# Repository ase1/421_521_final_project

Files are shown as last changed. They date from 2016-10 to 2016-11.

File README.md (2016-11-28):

# Kenny Toastman and Andrew Crusty present: [LaserToasterino](http://www.naminum.com/append?q=laser%20toaster)
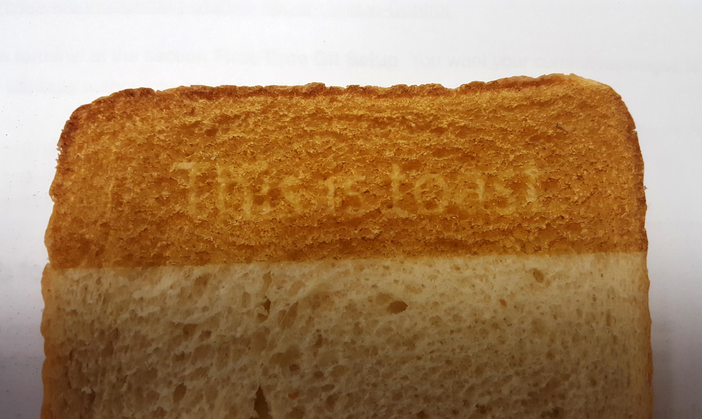
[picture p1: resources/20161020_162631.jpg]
This is toast.


This repository contains source code, CAD files, course deliverables, and instructions to create a laser toaster using a slew of microcontrollers. This is our final project for BIOE 421 at Rice University, taught by Dr. Jordan Miller and trusty assistant Dan Sazer. 

### Table of Contents
1. [Abstract] (#abstract)
2. [Use Flowchart] (#flowchart)
3. [Software Approach] (#software)
4. [Hardware Approach] (#hardware)
5. [Brainstorming] (#brainstorming)
6. [Safety] (#safety)

<a name="abstract">
### Abstract
Technological breakthroughs in the last decade have significantly altered the way we experience our everyday lives, from smartphones, smart TV's, and even IoT products like thermostats. One aspect of our lives, though, has not seen any improvements coming from technology for many decades-- toast. The goal of this project is to thrust the breakfast experience into the 21st century. We will create a device that allows you to wake up to a perfect piece of personalized toast. Laser etching will be used to burn images, a daily agenda, an inspirational quote, or the day’s headlines right onto a piece of bread. The device can be used immediately on command, or can be scheduled to have your perfect toast ready for you, right when you wake up. The image to be printed could be a selfie (or other inferior photo) that you upload or content from the Internet, allowing for an entirely customizeable breakfast.

The device will be comprised of a laser, an enclosure with controls, and a Raspberry Pi retrofitted onto an old 3D printer. Stepper motors will control the position of the laser along the toast, and the power of the laser will be modulated at each point to create different toasting patterns. Software will be developed to combine photos, Web-scraped text, and more into a grayscale image to be burned on the toast, and it will then generate G-code for printing. This project will aim to recreate the toaster experience using an Arduino to control the knobs, dings, and doors that we’ve all grown to love.

<a name="flowchart">
### Use Flowchart
This flowchart shows the processes and decisions that are made to output the admittedly scrumptious final product. 
Flowchart Flowchart showing use cases.

<a name="software">
### Software Approach
The three main facets of the software are controlling the motors/laser, generating and processing images for toasting into G-code, and displaying a graphical user interface to allow the user to select what they want on their toast. 

The GUI is the central hub of the software, connecting all of the pieces together. It runs in the Processing Development Environment, and monitors the touchscreen for button presses and acts accordingly. Each button is hardcoded because we didn't want to waste time making something fancy - we just need something that works. The GUI was laid out in Microsoft PowerPoint, then the layout was transferred over to Processing by determining all of the button sizes and locations. Screenshots of the GUI (running on a separate computer) are below: 

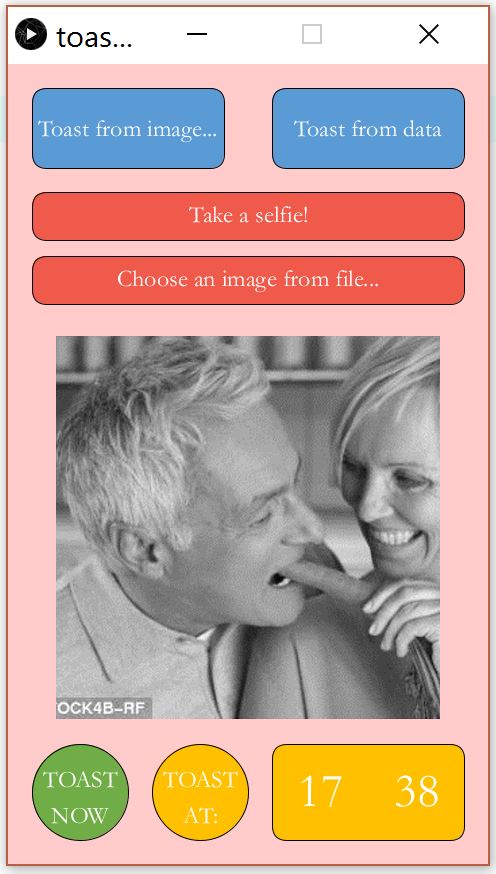
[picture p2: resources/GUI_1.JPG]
GUI1 Toast from an image...

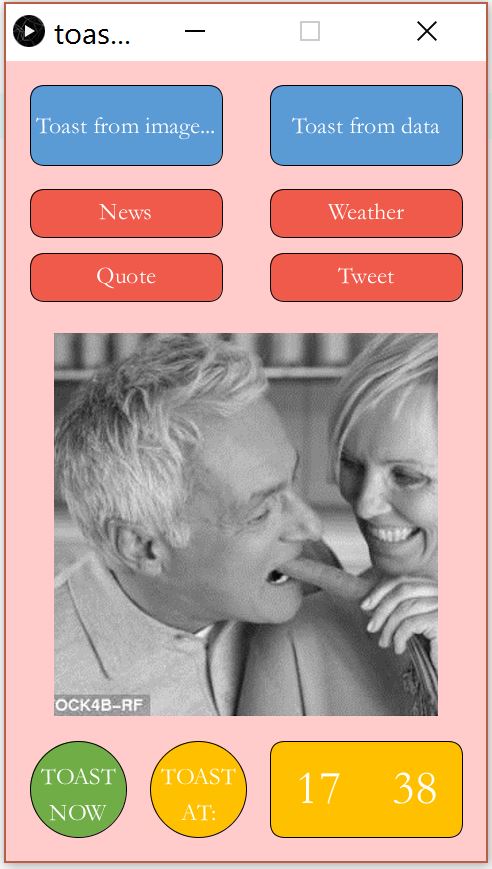
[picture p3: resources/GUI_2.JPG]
GUI2 Toast from data...

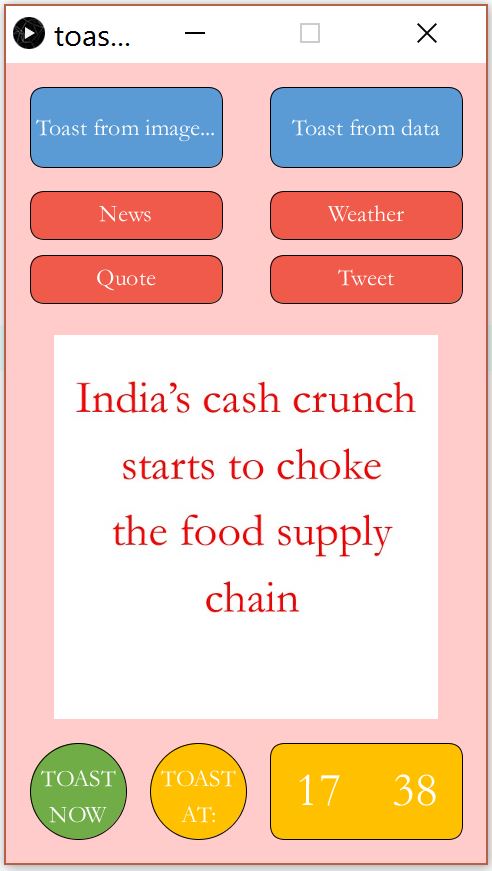
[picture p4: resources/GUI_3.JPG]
GUI3 Toast from data, populated


The GUI forces the user to follow the steps on the flowchart above, first prompting the user to either choose to toast from image or data, then prompting the user to select the specific pattern to toast. The user can either take an image using the Raspberry Pi camera, or use an existing file by navigating through the file browser. The toast from data option grabs the latest tweets from Twitter based on the selection, and formats the text as an image. The user then opts to immediately send the image to the toaster for processing and toasting, or to wait until the specified time. 

Each button press runs a bunch of scripts. We're using the launch() function in Processing, and launching .desktop files that run bash scripts that either run terminal functions or Python scripts. It's a really roundabout way of doing things, but it's the way we've been able to make Processing work for us. Variables for other scripts (like the image path, scheduled time, or status of the emergency stop button) are stored in dedicated text files. We chose to use Processing for the GUI environment because we want to integrate Arduino StandardFirmata and also want to make an attractive layout for the touchscreen. 

Once a user is ready to make his toast, he initiates a printing sequence by selecting the "Toast Now" button on the GUI. This actuates a series of steps that lead to printing, all executed in Python:

1. *Image Processing:*
  * Image resized to 128 x 128 pixels, which are the dimensions of the print (these numbers could change based on testing)
  * Image recolored to grayscale with lighter colors corresponding to darker pixels
    * This is so that lighter images will be more toasted
    * RGB values are converted to grayscale using a weighted average formula: I = .299[R] + .587[G] + .114[B]
  * Grayscale values are scaled to a power level 0-255, corresponding to the PWM range of the RAMBo Fan MOSFET output
    * Scaling is also based on the user's deisred toast power level (provided through the potentionmeter knob and Arduino)
    
2. *Automatic G-Code Generation:*
  * Based on the printer's print-area coordinates, the code generates a path for the laser head that covers each pixel in the image
  * At each pixel, the laser intensity changes corresponding to the intensity at that pixel
  * At the end of the print, the platform returns the toast to the user.
  * The G-Code is generated and saved as a .gcode file 
  
3. *Communicating with the Printer:*
  * We use Printcore, a software developed by Printrun (same group that makes Pronterface, Pronsole), to communicate with our RAMBo board.
    * Printcore is developed in Python and includes a module of commands that allow a user to interact with a printer
  * Connect with the printer through Serial Port, send over the G Code, and initiate print.
  * For safety, we also added the capability for a user to cancel the print mid-print, using the red "X" button in the GUI    

<a name="hardware">
### Hardware Approach
We have an old 3D printer, inherited from legendary Rice alum Ravi Sheth. We're using this as the base of our project since it already has the dimensional movement that our plotter will require. We want to take apart the printer, remove unnecessary components, and reassemble it inside of an enclosure. We need to install a couple of Arduino-controllable actuators to put some polish on the experience. For EHS reasons, we aren't allowed to use a laser powerful enough to cause blindness, so as a proof of concept, we'll mount a 5mW laser on the machine and test using photographic paper. 

The modified 3D printer hardware was modelled in SolidWorks, and the enclosure was created around it. The enclosure is made of plywood, which is fine for now because the laser isn't powerful enough to burn through it. It was made in the OEDK woodshop, and the display panel was ironically cut using a lasercutter. For the interface with the user, we're using a Raspberry Pi touchscreen display and a couple buttons and knobs for tactile control. A sliding door will shield the user from the laser during operation. 

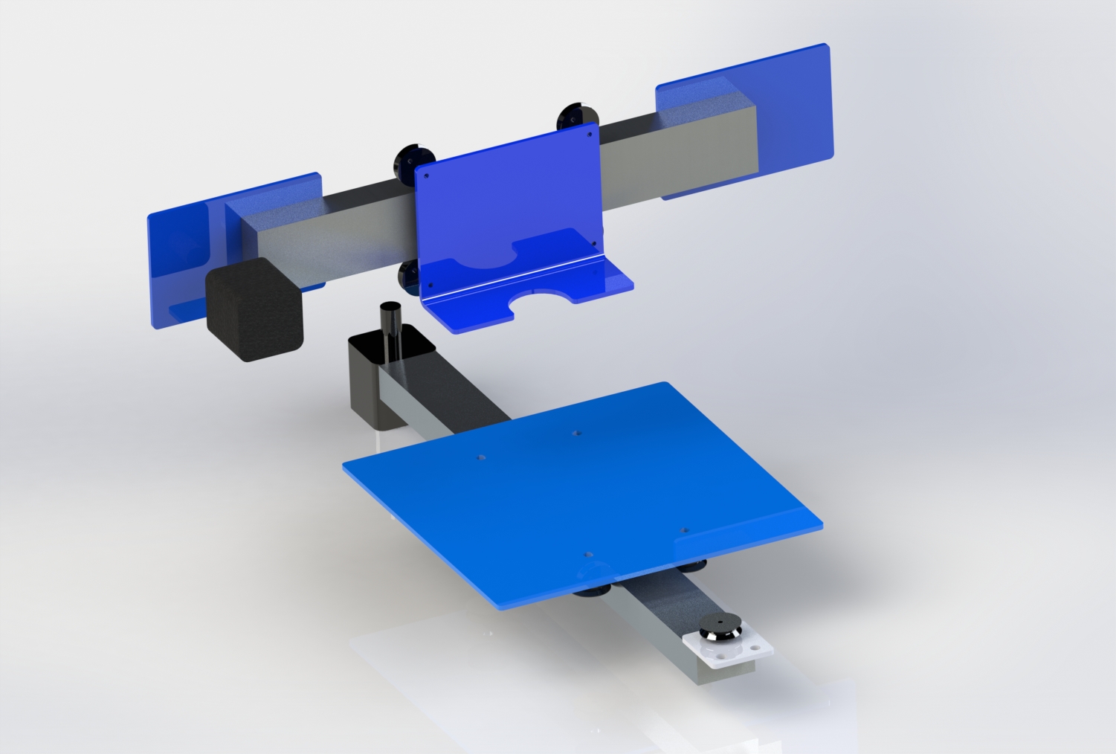
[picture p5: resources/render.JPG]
rendering The salvaged 3D printer parts


On the electrical side, we'll be using three boards for this project: a Raspberry Pi, a RAMBo motherboard, and an Arduino Uno. We had a bunch of problems hooking up the laser to the RAMBo; the idea was to control the intensity using the 12V PWM slot for cooling fans, but the fuses on the board kept burning out when our 5V lasers were connnected. We made a linear voltage regulator circuit to control the input voltage to the laser diode, and it seems to be more stable now. Both the Arduino and the RAMBo communicate with the Raspberry Pi using a serial connection. The Pi connects directly to the touchscreen and uses that as the only display. Ideally, the keyboard and mouse will be unnecessary to run the printer. 

<a name="brainstorming">
### Brainstorming
We spent the weekend coming up with ideas, and the crowd favorite is a toast printer. You've seen Jesus toast, and we want to take that one step further. Imagine waking up, checking your calendar, reading the newspaper, and ravenously scrounging for something to eat in the morning. Our idea proposes to combine early morning activities using a toaster with a controllable toast pattern. We're considering creating an appliance that internally works like a laser etcher, with the functions of a toaster. We have a non-working 3D printer that we're willing to scavenge for parts. We plan to design the hardware and software experience. Software for generating G-code for laser etching already exists, so we'd probably implement that and focus our efforts on image processing, content production, and hardware control. 

 - Sensors: 
   - Check if bread is on the plate
   - Check door status (open/closed)
   - Check power level dial
   - Button for start
   - Laser temperature

 - Actuators: 
   - Emergency stop button
   - Eject button (might be fun to have this under a plastic shield)
   - Must include spring actuation and self-deployed toast parachute
   - Move platform
   - Open/close door
   - Ring bell when complete
   - Laser ventilation
   - Alarm clock function that wakes you up to fresh toast

 - If we have time (we won’t have time):
   - Toast flipper
   - Camera on toast (timelapse?) (Twitter?)
   - Butter melter and liquid butter spreader
   - Photo booth

##### Discrete subprojects: 
 - Create lasercutter functionality - hardware
   - Disassemble printer
   - Buy parts
   - Figure out power requirements
   - Safety measures
   - Control 
 - Data grabbing from the internet
   - Date
   - Inspirational quotes
   - News
   - Notifications
 - Compile into an image for image processing
   - Image processing (see this: http://nebarnix.com/img2gco/)
   - Take existing image and convert to grayscale
   - Create an array of laser voltages per pixel
     - We can just always go line-by-line if that’s easier
   - Send to laser cutter
   - Arduino stuff

<a name="safety">
### Safety (for a device with a full-powered laser)
We can break safety concerns down to three categories: health, fire, and electrical. 

__Health__. The most threatening safety concern is health - pointing a laser at a person for too long could cause blindness or burns. The easiest countermeasure is to buy the lowest-powered laser that will still accomplish our goal. We're ready to do some testing on Thursday using the OEDK laser cutter to see what powers we realistically need for etching the toast, but online research has shown that we won't need more than 1-2 W. For testing, we'll want to modulate that power down to the mW range (typical laser pointers are 5-10 mW) so we can see what we're doing but aren't creating any threat. The final device will have a door that seals the inside off from the outside, so there can be no leakage of light. We can make this door into a physical switch, so the laser can't receive power unless this door is closed. For testing, we'll also have to get some laser safety glasses, which depend on the wavelength of light produced by the laser. 

__Fire__. Another big one, also mostly solved by choosing the right laser. We want to do some testing on the laser that we eventually choose, but if need be, we can solder on a heatsink and provide forced convection with a fan. I don't expect there to be too much smoke produced, since normal toasters don't produce an unreasonable amount of smoke and we plan to only etch the surface of the toast. We want to make the enclosure out of think aluminum or 1/4" wood - the laser shouldn't be high-powered enough to penetrate or ignite either of these. 

__Electrical__. Good insulation practices should resolve any concerns.

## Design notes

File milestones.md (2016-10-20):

# Toastr (name pending) Milestones
Andrew Elsey, Kenny Groszman
BIOE 421

Here we will outline our deadlines that we hope to accomplish in order to finish this project on time.

### Class Due Dates:
 - Abstract : 11/3
 - Initial Proof of Concept Prototype : 11/10
 - Fit and Finish : 11/17
 - Final project Due : 11/29

Milestones:

 - 10/27 :
   - CAD Model of Hardware and generate list of parts to acquire (Andrew)
   - Image processing software (Kenny)
      - Importang an image, resizing it, converting to grayscale, exporting matrix of power levels
   - Take apart 3D printer
   - Lay out structure of software and what functions we need, how they fit together, etc.

 - 11/3 : 
   - Hardware: Retrofit laser to printer,  control location of laser using motors and necessary software, build enclosure
   - Software: generate the software that allows us to modulate motors and laser power
   - Finalize abstract (due 11/3!)

 - 11/10 : 
   - Go to EHS laser safety meetings?????????? on 11/4
   - Implement actuators and sensors (knobs, buttons, switches, dingy speaker)
   - Begin work on GUI
   - Try data scraping from the internet!
   - MUST HAVE INITIAL PROTOTYPE DUE BY 11/10

 - 11/17
   - Error handling
   - Streamline GUI
   - Turn in fit and finish, whatever that is
   - Try photopapaer experiments

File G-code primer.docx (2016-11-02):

GCODE Primer for Laser Cutter Control

General Information

Gcode is a very simple code designed to control 3D printers. We have an adapted version of a GCODE interpreter courtesy of Tim Schmidt from the Lansing Makers Network (https://github.com/lansing-makers-network/buildlog-lasercutter-marlin) that has been augmented to better control laser based machines like our laser cutter.

The flow of Gcode is fairly simple. Commands are given line by line with appropriate arguments. For example, a typical move command would look like this:

“G0 X1 Y2 Z3 F1000”

The initial command G0 specifies the function G0 to be applied. The following arguments are comprised of an initial letter to describe the type of argument, and a numerical value to quantify the argument. For example, the letters X, Y, and Z denote coordinates in the X, Y, and Z directions respectively. The numbers following X, Y, and Z show the coordinate value to move towards. The F value is a different argument, which specifies the movement speed. So 1000 quantifies how fast to move for this variable.

The Gcode RepRap wiki (http://reprap.org/wiki/G-code) gives a fairly comprehensive list of Gcode commands and appropriate descriptions. There are different Gcode interpreters including our interpreter (Marlin).

Interpreter firmware/Gcode syntax has been extensively used by the RepRap community to simplify the ability to control 3D printing movement. It is important to note though, that Gcode simply encodes for firing of electrical pulses in a predefined manner. So, even though Gcode was not designed for controlling a laser cutter, commands can be co-opted for unorthodox uses if the controller board is correctly wired to the laser cutter.

Below is a list of Gcode commands specific to our laser cutter/Marlin firmware setup with accompanying arguments and descriptions.

Important Commands for Controlling our Firmware

  - M649
    - Set Laser Fire Settings
    - Arguments
      - S
        - Laser Intensity
        - Values are 0 to 100 (float type)
        - Units are % laser power
      - L
        - Duration of laser pulse
        - Values are integers
        - Units are microseconds (μs)
      - P
        - Pulses per millimeter
        - Values are float type
        - Resolution discussed below
      - B
        - “Beam type”
        - 0 for continuous fire
        - 1 for Pulsed (note: specifying “P” should automatically change to B1 mode)
        - 2 for raster mode
      - D
        - Diagnostics
        - Logical 0 or 1 for whether to output diagnostics
  - M3
    - Turn laser on with current laser settings
    - Laser settings can be specified with an M3 command, but if a setting is not specified, the previously used value will be used.
  - M5
    - *****Turn laser off
  - G0
    - Move without laser on
    - Behaves identically with old marlin Gcode
  - G1
    - Move with laser on
    - Uses previously stored laser settings
    - Can take arguments from M649 to customize laser settings
  - M114
    - Obtain current coordinates
    - Enter directly to pronterface
    - Can be input while printing without disrupting the current print
  - G92
    - Set Coordinates
    - Takes X, Y, and Z arguments
  - G90
    - Set absolute coordinates
    - G0/G1 commands with X, Y, and Z will specify absolute coordinate locations
    - i.e. if you enter G0 X1 Y2 Z3 twice, the first command will move to (1,2,3) and the second command will not move (because you are already at the specified locations)
  - G91
    - Set relative coordinates
    - G0/G1 commands with X,Y, and Z will specify a relative movement direction
    - i.e. G0 X1 Y2 Z3 twice will move in a <1,2,3> vector direction twice to a final destination of (2, 4, 6) relative to the initial position
  - M84
    - Turn motors off

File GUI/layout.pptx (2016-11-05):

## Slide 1

Toast from image

Toast from data

Take a selfie!

Choose image…

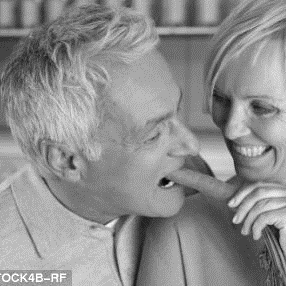
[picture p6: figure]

TOAST NOW

TOAST
AT:

08

15

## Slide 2

Toast from image

News

Agenda

Toast from data

Quote

Latest tweet from…

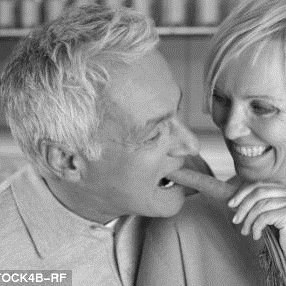
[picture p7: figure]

TOAST NOW

TOAST
AT:

08

15

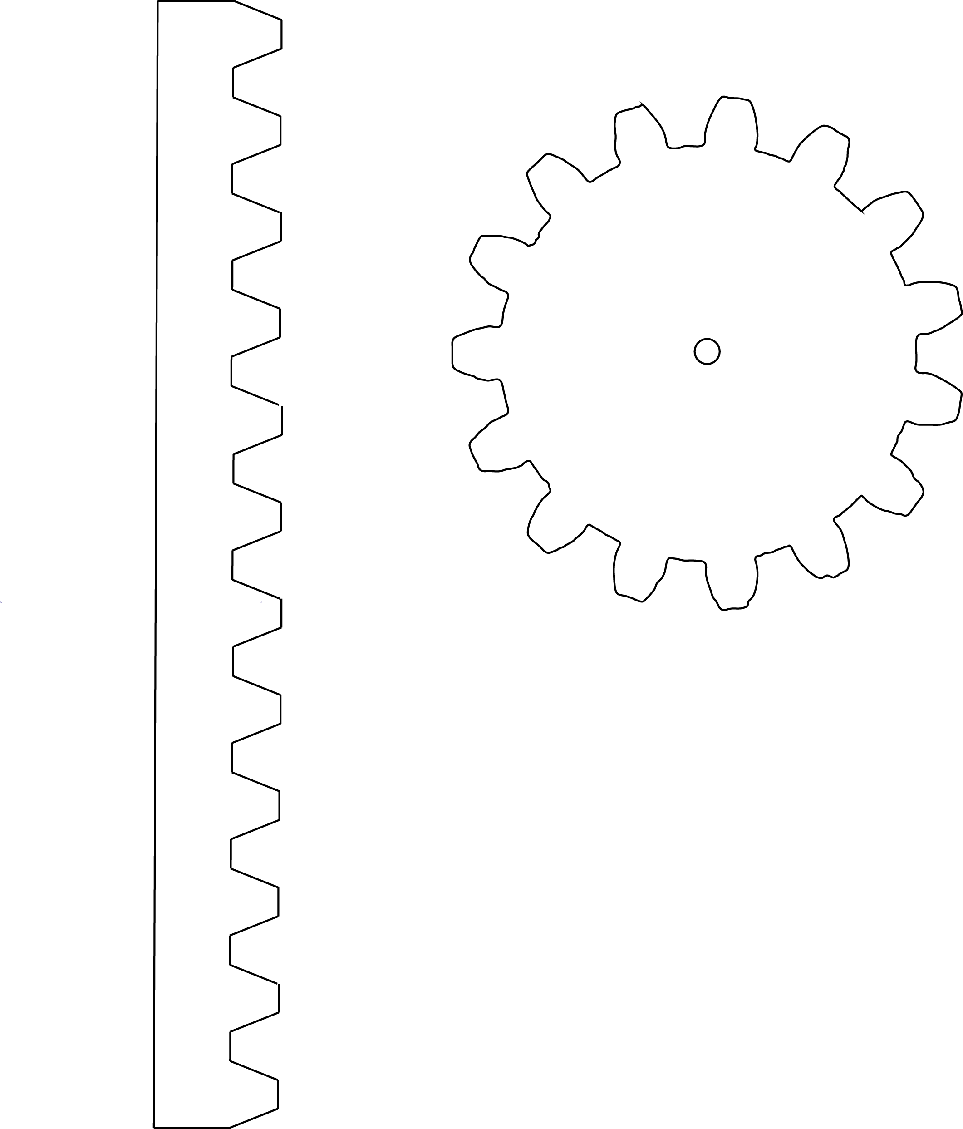
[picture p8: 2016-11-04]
Hardware/gears.png

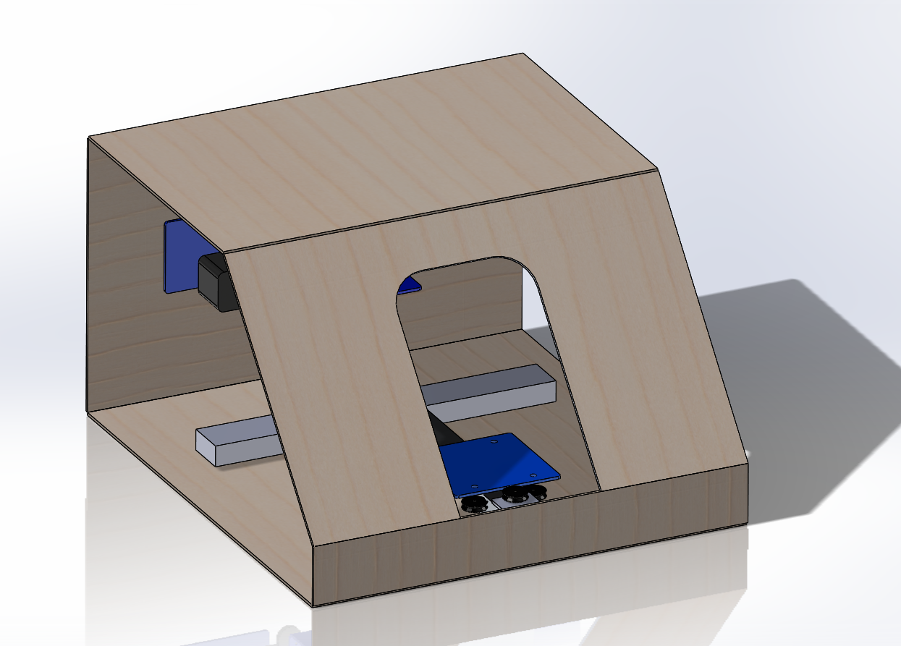
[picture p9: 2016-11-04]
Hardware/enclosure.PNG

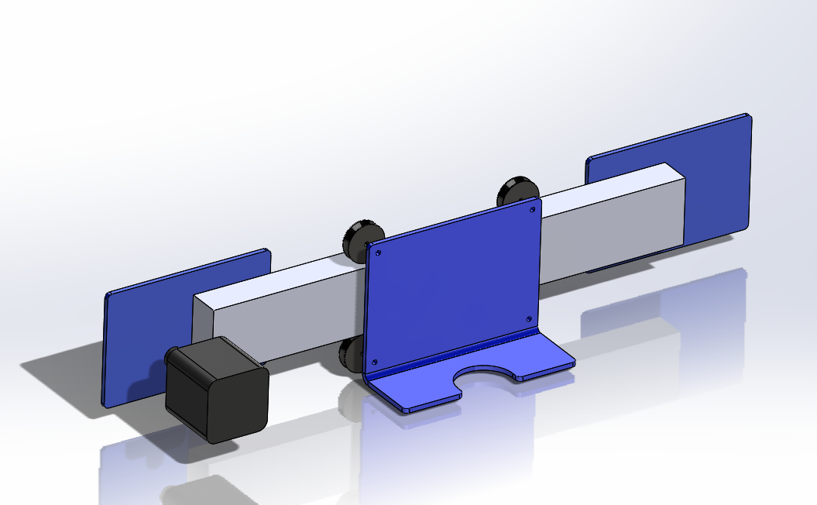
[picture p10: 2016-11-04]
Hardware/laser_assy.PNG

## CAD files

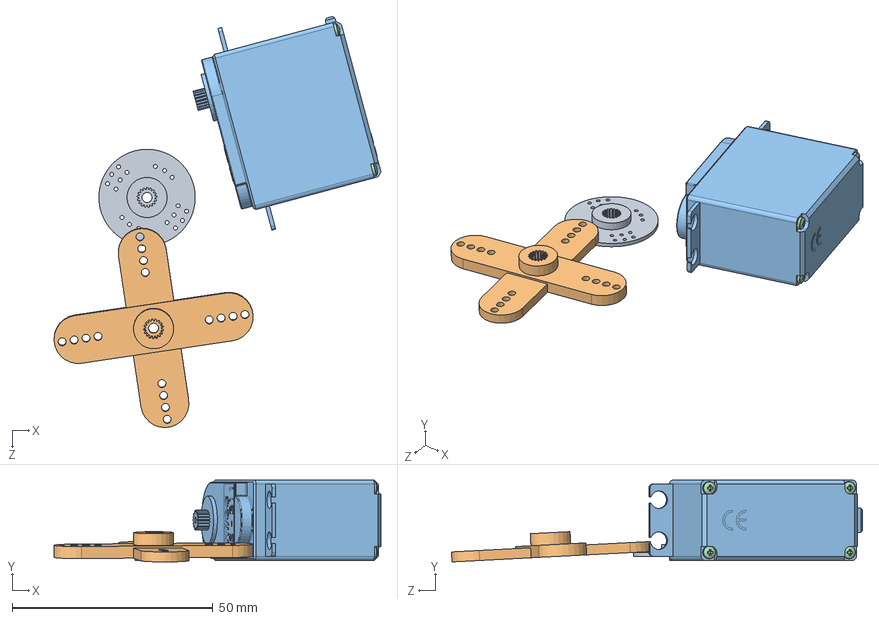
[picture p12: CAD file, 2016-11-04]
Hardware/Hitec HS-311 Servo Motor/Hitec HS-311.SLDASM
81.4 x 20.4 x 102.3 mm
Spline
Spline 2
Hitec Servo Motor HS-311
pan head cross recess screw_din x 4

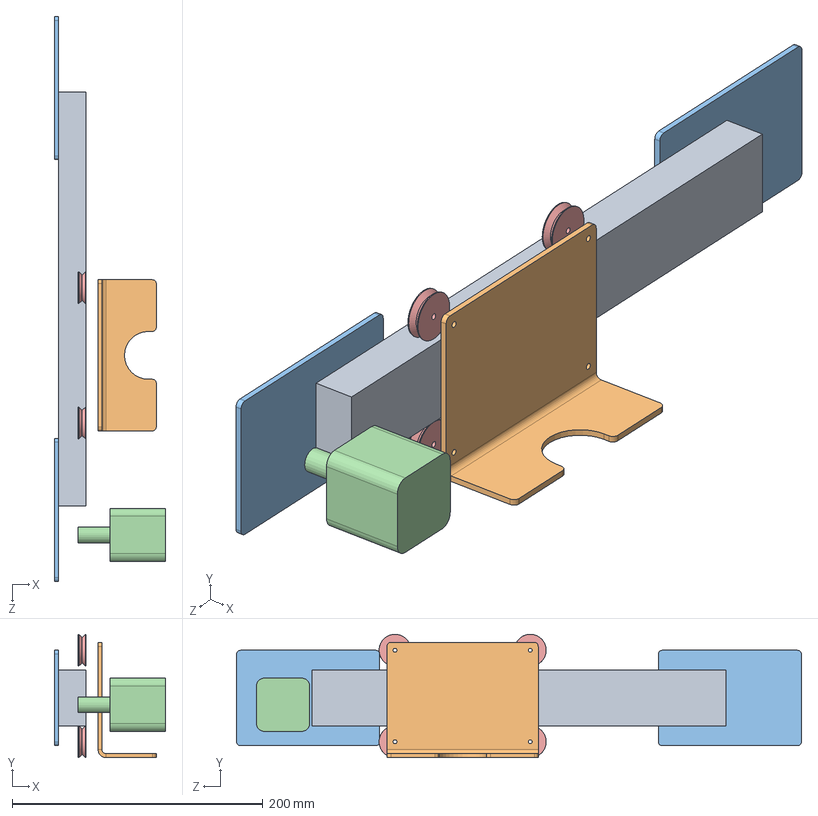
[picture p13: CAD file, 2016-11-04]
Hardware/laser_assy.SLDASM
88.9 x 98.4 x 450.9 mm
topchannel
lasermount
supportplate x 2
motor
bearing x 4

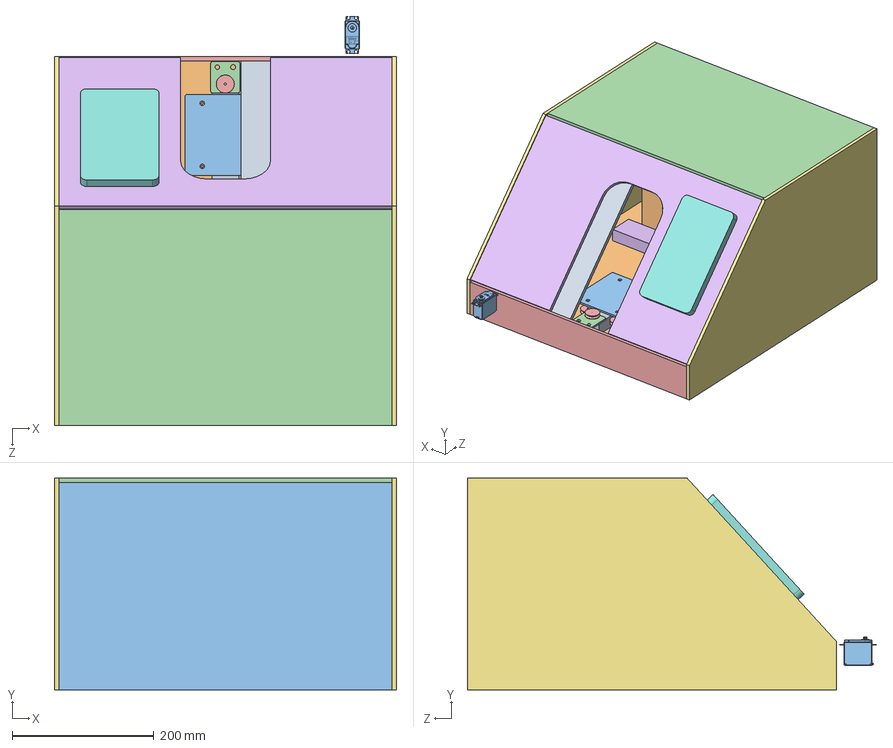
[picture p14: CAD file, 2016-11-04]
Hardware/full_assy.SLDASM
482.6 x 298.5 x 576.8 mm
bottomchannel
motor x 2
platformnew
frontplate
bearing x 9
basechannel
topchannel
lasermount
supportplate x 2
enc_base
enc_back
enc_top
enc_front
enc_display
enc_side x 2
raspi screen
enc_door
supportchannel x 2
Hitec Servo Motor HS-311

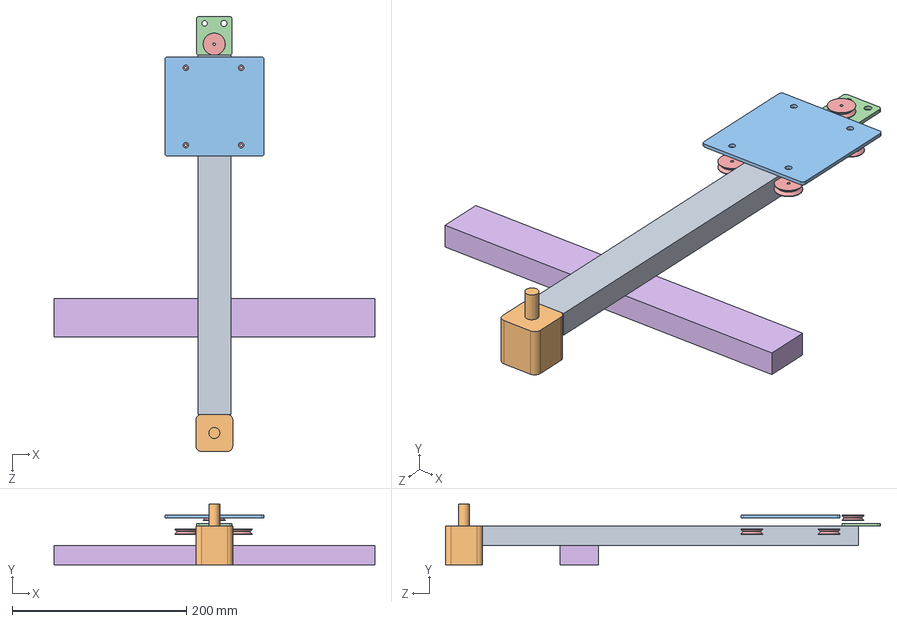
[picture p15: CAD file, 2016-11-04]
Hardware/bottom_assy.SLDASM
368.3 x 69.8 x 499.7 mm
bottomchannel
motor
platformnew
frontplate
bearing x 5
basechannel

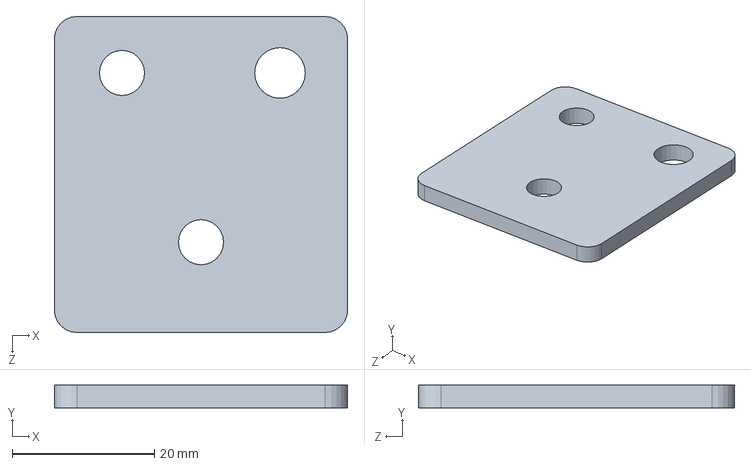
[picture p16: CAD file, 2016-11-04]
Hardware/frontplate.SLDPRT
41.3 x 3.17 x 44.5 mm

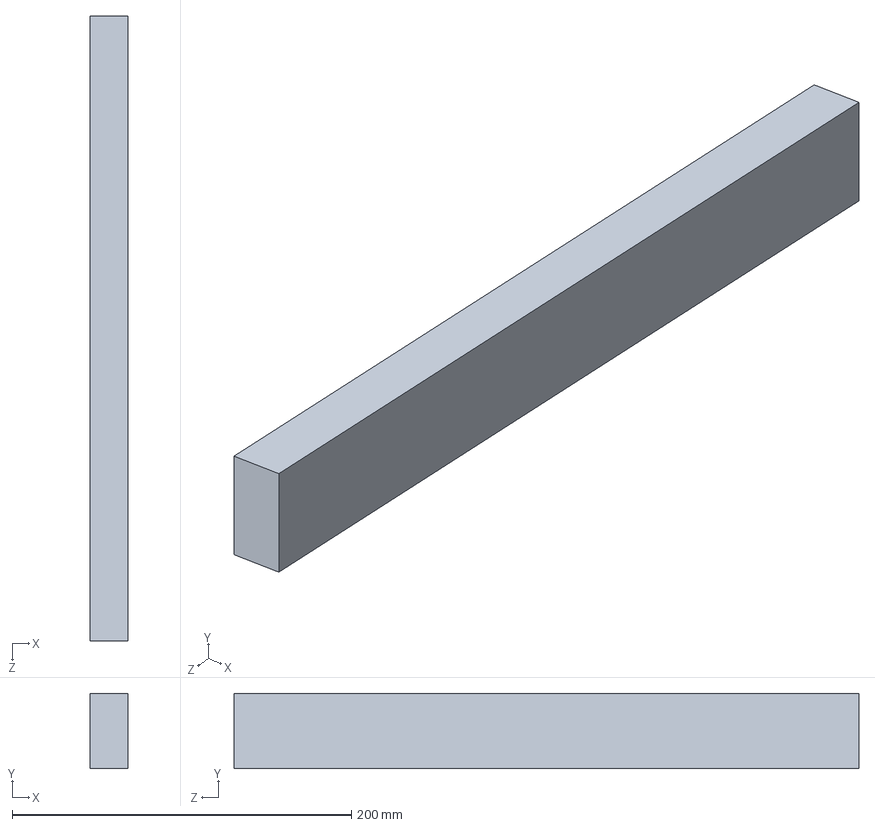
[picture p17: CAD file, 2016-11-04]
Hardware/basechannel.SLDPRT
22.2 x 44.5 x 368.3 mm

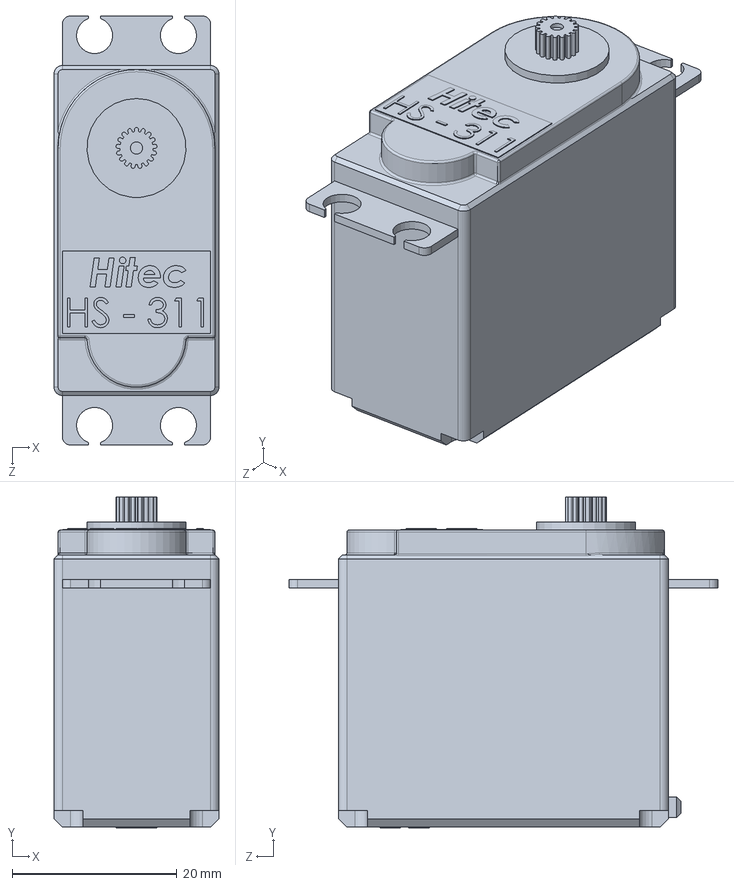
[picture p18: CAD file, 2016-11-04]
Hardware/Hitec HS-311 Servo Motor/Hitec Servo Motor HS-311.SLDPRT
20.0 x 40.1 x 52.0 mm

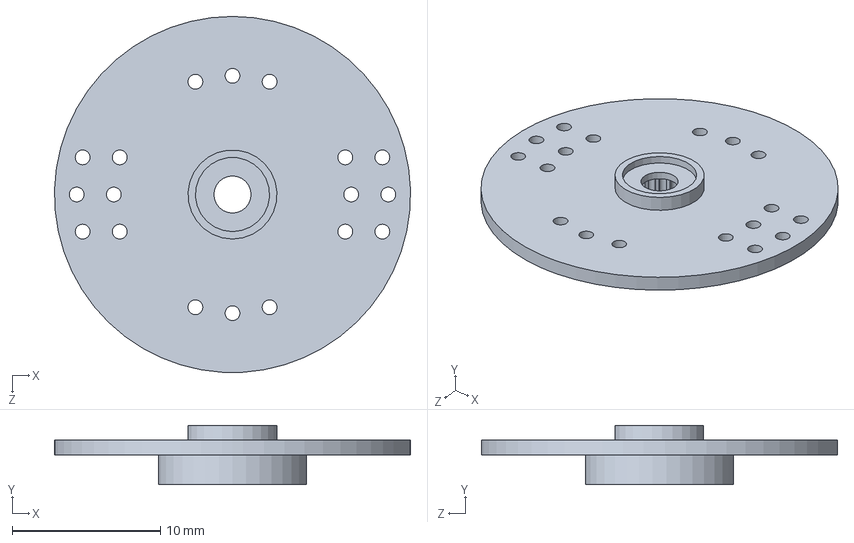
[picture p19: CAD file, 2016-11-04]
Hardware/Hitec HS-311 Servo Motor/Spline.SLDPRT
24.0 x 4.00 x 24.0 mm

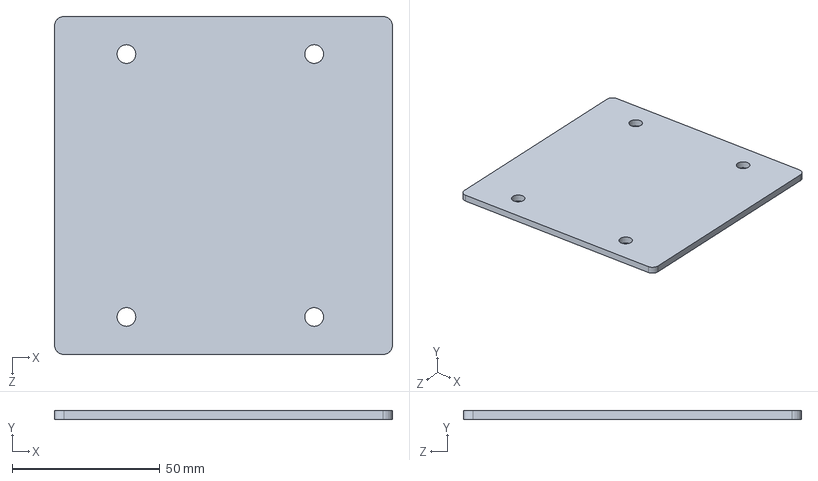
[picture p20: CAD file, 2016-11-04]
Hardware/platformnew.SLDPRT
114.3 x 3.17 x 114.3 mm

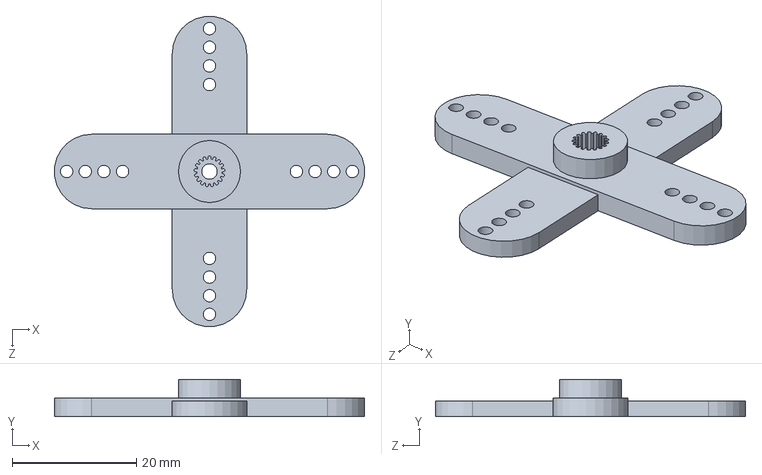
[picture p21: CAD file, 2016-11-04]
Hardware/Hitec HS-311 Servo Motor/Spline 2.SLDPRT
49.9 x 6.00 x 49.9 mm

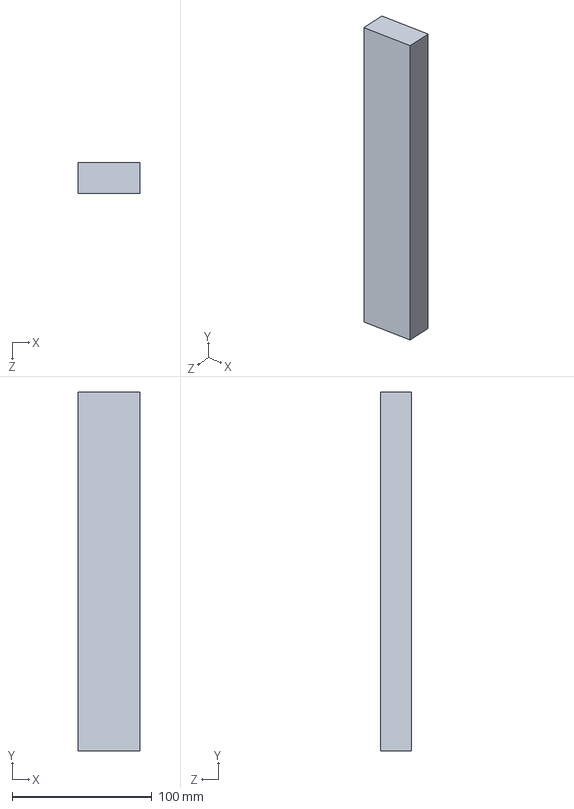
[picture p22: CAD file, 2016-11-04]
Hardware/supportchannel.SLDPRT
44.5 x 257.2 x 22.2 mm

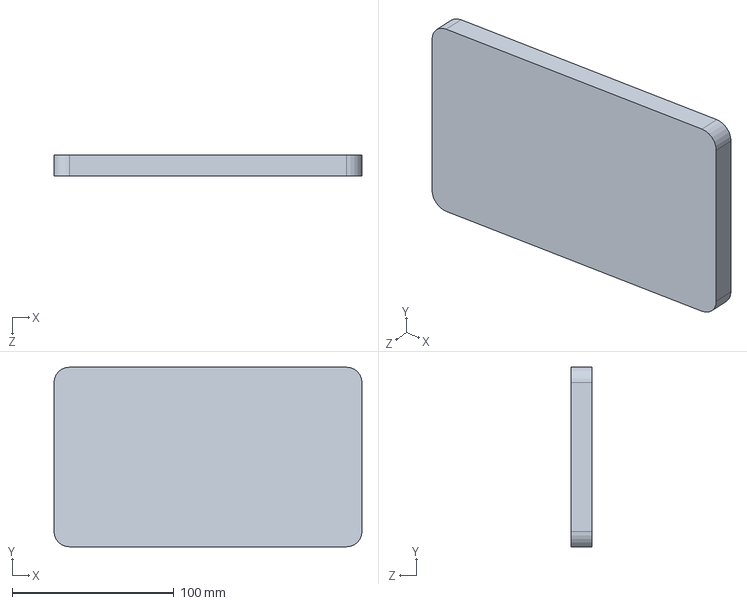
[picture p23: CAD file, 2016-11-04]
Hardware/raspi screen.SLDPRT
190.5 x 111.1 x 12.7 mm

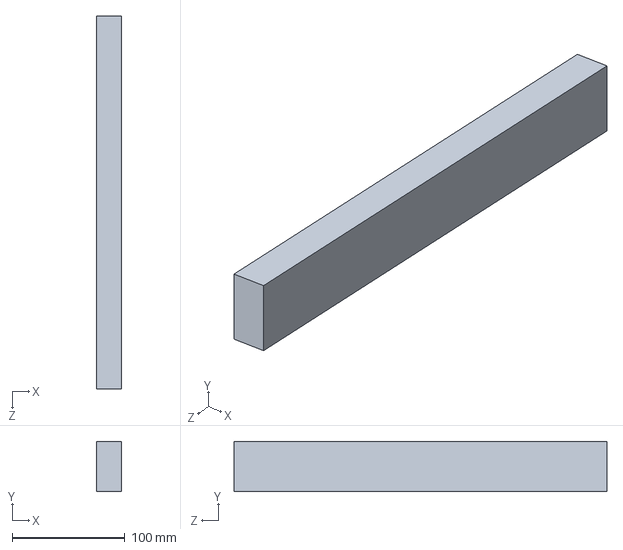
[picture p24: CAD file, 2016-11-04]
Hardware/topchannel.SLDPRT
22.2 x 44.5 x 330.2 mm

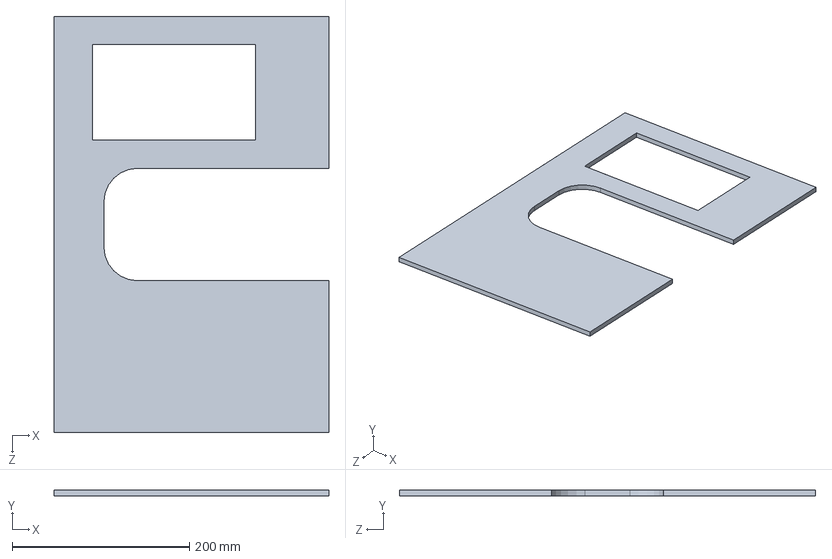
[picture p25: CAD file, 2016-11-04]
Hardware/enc_display.SLDPRT
310.1 x 6.35 x 469.9 mm

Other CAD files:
Hardware/enc_door.SLDPRT
Hardware/enc_front.SLDPRT
Hardware/supportplate.SLDPRT
Hardware/mount.SLDPRT
Hardware/bearing.SLDPRT
Hardware/bottomchannel.SLDPRT
Hardware/enc_back.SLDPRT
Hardware/enc_base.SLDPRT
Hardware/enc_side.SLDPRT
Hardware/enc_top.SLDPRT
Hardware/lasermount.SLDPRT
Hardware/motor.SLDPRT
Hardware/pinion.SLDPRT
Hardware/platform.SLDPRT
Hardware/rack_no_teeth.SLDPRT

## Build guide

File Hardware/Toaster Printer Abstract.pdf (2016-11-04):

Technological breakthroughs in the last decade have significantly altered the way we experience our everyday lives, from smart phones, smart TV's, and even IoT products like air conditioners. One aspect of our lives, though, that has not seen any improvements coming from technology for many decades-- toast. The goal of this project is to bring the breakfast experience to the 21st century. We will create a device that allows you to wake up to a perfect piece of personalized toast. Laser etching will be used to burn images, a schedule, an inspirational quote, or the day’s headlines right onto a piece of bread. The device can be set to act like an alarm clock, waking you up to your perfect toast, or used throughout the day. The image to be printed could be a selfie that you upload, data from relevant news websites, or updates from your favorite social media site, allowing for an entirely customizable breakfast.

The device will feature a laser, an enclosure with controls, and a Raspberry Pi retrofitted onto an old 3D printer. Stepper motors will control the position of the laser along the toast, with the power of the laser modulated at each point to create different toasting patterns. Software will be developed to combine photos, Web-scraped text, and more into a grayscale image to be burned on the toast, and process this image for printing. This project will aim to recreate the toaster experience using an Arduino to control the knobs, dings, and doors that we’ve all grown to love.

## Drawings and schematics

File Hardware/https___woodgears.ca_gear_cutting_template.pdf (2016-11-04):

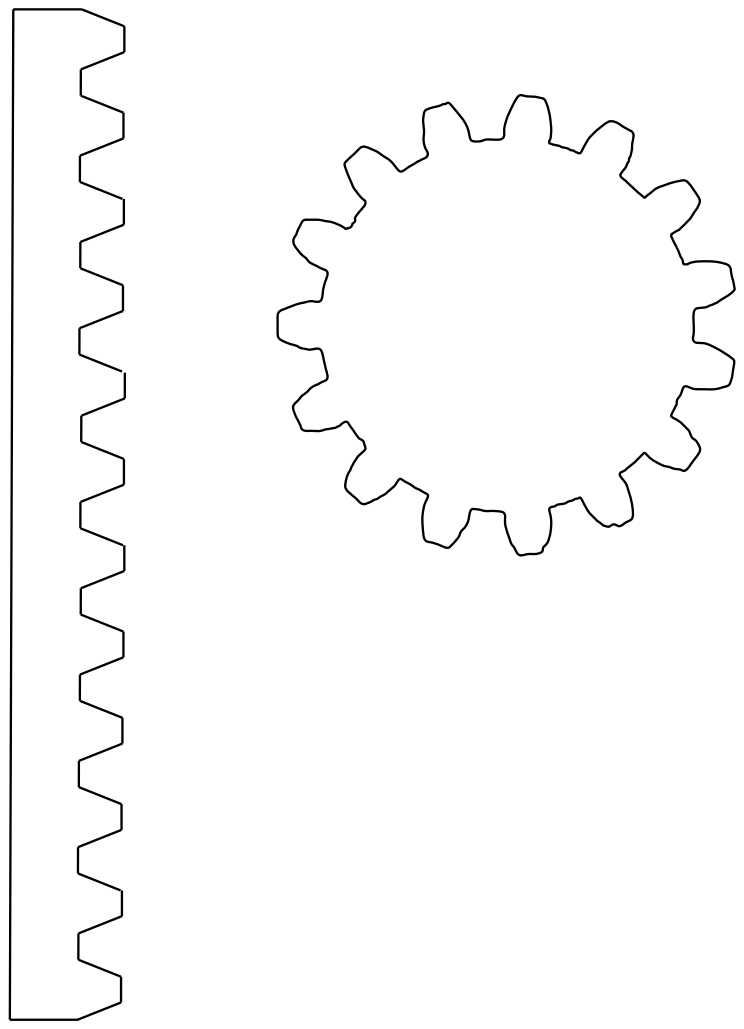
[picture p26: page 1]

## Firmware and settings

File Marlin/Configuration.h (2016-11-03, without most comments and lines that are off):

#define CONFIGURATION_H
#define STRING_VERSION_CONFIG_H __DATE__ " " __TIME__ // build date and time
#define STRING_CONFIG_H_AUTHOR "(ChenLab ShopBot Desktop D2418 by jmil, using Ultimachine RAMBo)" //Who made the changes.
#define SERIAL_PORT 0
#define BAUDRATE 250000
#define MOTHERBOARD 301
#define POWER_SUPPLY 1
#define TEMP_SENSOR_0 0
#define TEMP_SENSOR_1 0
#define TEMP_SENSOR_2 0
#define TEMP_SENSOR_BED 1
#define TEMP_RESIDENCY_TIME 10	// (seconds)
#define TEMP_HYSTERESIS 3       // (degC) range of +/- temperatures considered "close" to the target one
#define TEMP_WINDOW     1       // (degC) Window around target to start the recidency timer x degC early.
#define HEATER_0_MINTEMP 5
#define HEATER_1_MINTEMP 5
#define HEATER_2_MINTEMP 5
#define BED_MINTEMP 5
#define HEATER_0_MAXTEMP 275
#define HEATER_1_MAXTEMP 275
#define HEATER_2_MAXTEMP 275
#define BED_MAXTEMP 150
#define PIDTEMP
#define BANG_MAX 256 // limits current to nozzle while in bang-bang mode; 256=full current
#define PID_MAX 256 // limits current to nozzle while PID is active (see PID_FUNCTIONAL_RANGE below); 256=full current
  #define PID_FUNCTIONAL_RANGE 10 // If the temperature difference between the target temperature and the actual temperature
  #define PID_INTEGRAL_DRIVE_MAX 255  //limit for the integral term
  #define K1 0.95 //smoothing factor withing the PID
  #define PID_dT ((16.0 * 8.0)/(F_CPU / 64.0 / 256.0)) //sampling period of the temperature routine
    #define  DEFAULT_Kp 22.2
    #define  DEFAULT_Ki 1.08
    #define  DEFAULT_Kd 114
#define MAX_BED_POWER 256 // limits duty cycle to bed; 256=full current
#define PREVENT_DANGEROUS_EXTRUDE
#define PREVENT_LENGTHY_EXTRUDE
#define EXTRUDE_MINTEMP 170
#define EXTRUDE_MAXLENGTH (X_MAX_LENGTH+Y_MAX_LENGTH) //prevent extrusion of very large distances.
#define ENDSTOPPULLUPS // Comment this out (using // at the start of the line) to disable the endstop pullup resistors
  #define ENDSTOPPULLUP_XMIN
  #define ENDSTOPPULLUP_YMIN
  #define ENDSTOPPULLUP_ZMIN
const bool X_ENDSTOPS_INVERTING = false; // set to true to invert the logic of the endstops.
const bool Y_ENDSTOPS_INVERTING = false; // set to true to invert the logic of the endstops.
const bool Z_ENDSTOPS_INVERTING = false; // set to true to invert the logic of the endstops.
#define X_ENABLE_ON 0
#define Y_ENABLE_ON 0
#define Z_ENABLE_ON 0
#define E_ENABLE_ON 0 // For all extruders
#define DISABLE_X false
#define DISABLE_Y false
#define DISABLE_Z false
#define DISABLE_E false // For all extruders
#define INVERT_X_DIR true    // for Mendel set to false, for Orca set to true
#define INVERT_Y_DIR true    // for Mendel set to true, for Orca set to false
#define INVERT_Z_DIR true     // for Mendel set to false, for Orca set to true
#define INVERT_E0_DIR false   // for direct drive extruder v9 set to true, for geared extruder set to false
#define INVERT_E1_DIR false    // for direct drive extruder v9 set to true, for geared extruder set to false
#define INVERT_E2_DIR false   // for direct drive extruder v9 set to true, for geared extruder set to false
#define X_HOME_DIR -1
#define Y_HOME_DIR -1
#define Z_HOME_DIR -1
#define min_software_endstops false //If true, axis won't move to coordinates less than HOME_POS.
#define max_software_endstops true  //If true, axis won't move to coordinates greater than the defined lengths below.
#define X_MAX_POS 600
#define X_MIN_POS 0
#define Y_MAX_POS 475
#define Y_MIN_POS 0
#define Z_MAX_POS 90
#define Z_MIN_POS 0
#define X_MAX_LENGTH (X_MAX_POS - X_MIN_POS)
#define Y_MAX_LENGTH (Y_MAX_POS - Y_MIN_POS)
#define Z_MAX_LENGTH (Z_MAX_POS - Z_MIN_POS)
#define MANUAL_X_HOME_POS 0
#define MANUAL_Y_HOME_POS 0
#define MANUAL_Z_HOME_POS 0
#define NUM_AXIS 4 // The axis order in all axis related arrays is X, Y, Z, E
#define HOMING_FEEDRATE {50*60, 50*60, 50*60, 0}  // set the homing speeds (mm/min)
#define DEFAULT_AXIS_STEPS_PER_UNIT   {78.7402,78.7402,200.0*8/3,760*1.1}  // default steps per unit for ultimaker
 #define DEFAULT_MAX_FEEDRATE          {500, 500, 5, 25}    // (mm/sec)
 #define DEFAULT_MAX_ACCELERATION      {9000,9000,100,10000}    // X, Y, Z, E maximum start speed for accelerated moves. E default values are good for skeinforge 40+, for older versions raise them a lot.
 #define DEFAULT_ACCELERATION          3000    // X, Y, Z and E max acceleration in mm/s^2 for printing moves
 #define DEFAULT_RETRACT_ACCELERATION  3000   // X, Y, Z and E max acceleration in mm/s^2 for r retracts
 #define DEFAULT_XYJERK                20.0    // (mm/sec)
 #define DEFAULT_ZJERK                 0.4     // (mm/sec)
 #define DEFAULT_EJERK                 5.0    // (mm/sec)
#define PLA_PREHEAT_HOTEND_TEMP 180
#define PLA_PREHEAT_HPB_TEMP 70
#define PLA_PREHEAT_FAN_SPEED 255		// Insert Value between 0 and 255
#define ABS_PREHEAT_HOTEND_TEMP 240
#define ABS_PREHEAT_HPB_TEMP 100
#define ABS_PREHEAT_FAN_SPEED 255		// Insert Value between 0 and 255
#define BARICUDA
#include "Configuration_adv.h"
#include "thermistortables.h"

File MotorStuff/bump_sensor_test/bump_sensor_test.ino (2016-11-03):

int bump;

void setup() {
  // put your setup code here, to run once:
  Serial.begin(9600);           // set up Serial library at 9600 bps

  pinMode(2, INPUT);
  pinMode(3,OUTPUT);
  digitalWrite(2, HIGH);
}


void loop() {
  // put your main code here, to run repeatedly:
  bump=digitalRead(3);
  
  Serial.println(bump +" "+ digitalRead(2));
 
  
}

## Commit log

2016-10-20 Added lasered toast image
    "This is toast."
2016-10-27 add GIF of proof-of-concept moving motor
2016-11-02 update code to flatten image matrix in proper order for printing.
    Need to update to make it output G Code
2016-11-03 add original marlin firmware
    [Configuration.h, Configuration_adv.h]
2016-11-03 ADD NEW VERSION OF MARLIN THAT WORKS!!!!!!!!!!!!!!!!!!!!!!!!
    [Configuration.h, Configuration_adv.h]
2016-11-03 upload working MARLIN
    [Menu Plans.xlsx]
2016-11-03 added CAD files for the updated design
2016-11-04 extracted and filed the CAD files for the hardware
2016-11-04 added unversioned CAD files
    [Hitec HS-311.SLDASM, Hitec Servo Motor HS-311.SLDPRT, Spline 2.SLDPRT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]
2016-11-04 moved resources to a resources folder, added flowchart.png
2016-11-05 added GUI folder and layout powerpoint
2016-11-05 started writing the GUI, laid out button locations
2016-11-06 added more GUI functionality: button presses, toast scheduling, image display
2016-11-06 improved GUI - added different toast modes and more buttons
2016-11-10 tried screwing with GUI in Pi
2016-11-15 generate images using GUI given data from internet, controlled by buttons
    working on making generated images always look good, regardless of number of characters
2016-11-15 fixed the non-working news thing by removing urls entirely.
    [toastGUI.pde]
2016-11-16 set backbone for connecting to printer
2016-11-16 integrated arduino, added power level functionality
2016-11-16 added legacy arduino library for processing
2016-11-16 testing connecting automatically with printre, fixerd issue with processiong not being able to run a bash script
    [excluder.py, gcodeplater.py, gcoder.py]
2016-11-16 upload a working version of printcore_test.py, which connects with and sends gcode to the rambo....
2016-11-16 move files to connect to printer into toastGUI folder
2016-11-16 update gcode generating code to include laser powers
2016-11-16 update gcode to turn laser off at end of print
2016-11-17 added a file "run_print2.py" which adds the functionality to pause a print while it is running. script still requires testing (and a bash script to run it), as well as a text file "stop_print.txt" to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
2016-11-17 added code to run all of the to-be-built Arduino stuff
2016-11-17 run print updates
2016-11-17 added printrun to GUI under print now
2016-11-17 calibrated laser moves
2016-11-17 push script from working fit and finish prototype. need to fix selfie anda automate execution...
    [toastGUI.pde]
2016-11-17 calibration of toast area
2016-11-22 removed delay() functions so that we have full control, made print function relative to millis(), animated toastmode=3
2016-11-22 prints scheduled time in toastmode 3, general improvements. note that launch functions are commented out
2016-11-22 added functionality to cancel the print in run_print2.py... still need to test w printer
2016-11-22 fixed a LOT of bugs
    [toastGUI.pde]
2016-11-22 fixed a bunch more bugs, including selfie compatibility
    [toastGUI.pde]
2016-11-29 update python to have power level functionality
2016-11-29 added CAD images
